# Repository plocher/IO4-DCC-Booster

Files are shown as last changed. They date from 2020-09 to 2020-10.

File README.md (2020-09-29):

# IO4-DCC-Booster
## License: CERN Open Hardware Licence v1.2

IO4 DCC Booster

A DIY DCC booster for a BOM cost of about $20 when using bulk China/eBay parts.

I was working on designing a motor shield using the $10 IBT-2
H-Bridge when I came across the work done by D. Bodnar at
[train electronics.com](http://www.trainelectronics.com/DCC_Arduino/DCC_Booster/)

I wanted to use one of these for every control point on my layout
instead of a DCC circuit breaker + booster power district mashup.
As the DCC Breakers are at least double the DIY cost for these
dedicated boosters, and I will end up with 10-20 control points on
my SPCoast layout, the savings might actually cover the development
costs :-)

These boosters DO NOT support auto-reverse, and the sketch software
doesn't try to do soft start detection of sound decoder capacitor
inrush currents.  Since there will be on average a single train
powered by each of these boosters on my N-Scale layout, I don't
expect this to be a real issue.  In practice, a simple 1 or 2 amp
unit would probably be good enough; at 5 to 6 amps, this is overkill.

From the original web writeup at trainelectronics.com:

<blockquote>
Introduction

In addition to experimenting with DCC++ over the last few months I
have been trying out different H-Bridges to see if there is one
that would work with DCC++ while delivering more than the 1 to 2
amps that the standard Arduino Motor Shield provides.  Such a option
would a good option for G scale layouts that typically draw much
more power than smaller scales.

I came across a few higher power shields
[that are described here](http://trainelectronics.com/DCC_Arduino/DCC++/)
including one that has an advertised power capability of 43 amps.
While I am a bit skeptical about this claim my tests show that it
has no problem delivering 5 or more amps, more than enough for my
purposes.  I describe how this can be interfaced to the DCC++
controller in the link above.

In order to make the use of this H-Bridge more convenient I decided
to design a stand-alone DCC booster that would attach to a DCC
signal and boost it before powering a track.  The booster is designed
to work with DCC++, Digitrax and other systems.

Hardware - H-Bridge

The H-Bridge is available from eBay, Amazon and other vendors -
just search for "H-Bridge 43 amp BTS7960B".  Make sure you get the
unit that has two BTS7960B devices on it - each is 1/2 of an H-Bridge.
The control signals go to the 8 pins on the front and the power in
and power out wires go to the 4 pin screw terminal connector at the
rear.

This H-Bridge and similar units do not operate on the single PWM
signal that most DCC systems provide.  It needs a right hand rotating
PWM and a left hand PWM.  To change the single PWM signal to two a
simple one transistor circuit is needed.  That circuit can be seen
in the lower left corner of the schematic (below).

The H-Bridge can act as a DCC booster without much more than the
Opto Coupler circuit and the one transistor converter.  The H-Bridge
does hove an over current shutdown capability but it doesn't react
until well over 30 amps are being drawn, way more than we are going
to use.  To get around this problem so that the system shuts down
immediately if the track is shorted an Arduino Pro Mini has been
added.  The Arduino monitors the current sensing pin on the H-Bridge
and can turn it off should it detect a high reading.

</blockquote>

His prototype reused a board he had on hand; this project simply
turns his schematic into a purpose-built board - and adds remote control
(enable/disable and monitoring) via an IO-4 RJ12/6 interface.

The differences:
  * powered by (3.0) the IO-4 Jack / IOexpander and (3.1) by the DC booster power.
  * local control - a maintainer "disable track power" switch
  * remote control
    * enable/disable track power
  * remote feedback
    * enabled
    * occupied
    * overload
  * Loconet and NCE Booster Bus daisy chain command station cable jacks

=== Estimated BOM costs ===
:	$ 1.00  PCB 
:	$10.00  IBT-2 
:	$ 3.50  Pro Mini Clone
:	$ 0.45  6n137
:	$ 0.20  2200uF x2
:	$ 3.00  RJ and Phoenix connectors
:	$ 1.00  SPDT Switch
:	$ 1.00  R/C/LEDs
:	------
:      ~$20.00

The booster will also need a 12-18v 6A+ DC power supply; the logic and
feedback electronics are isolated from the power supply (using opto
isolator for the booster bus and a full wave bridge for the power
supply), so there should be no problems driving a set of boosters
from a single large amperage switching supply.

As with ALL high power systems, use a SLOW BLOW or POLYFUSE in your
power supply feed.  20v at 6A is 120W - similar to a very bright
and hot incandescent bulb, if you remember them.  You don't want
to arc weld or start a fire on your layout if something goes wrong!

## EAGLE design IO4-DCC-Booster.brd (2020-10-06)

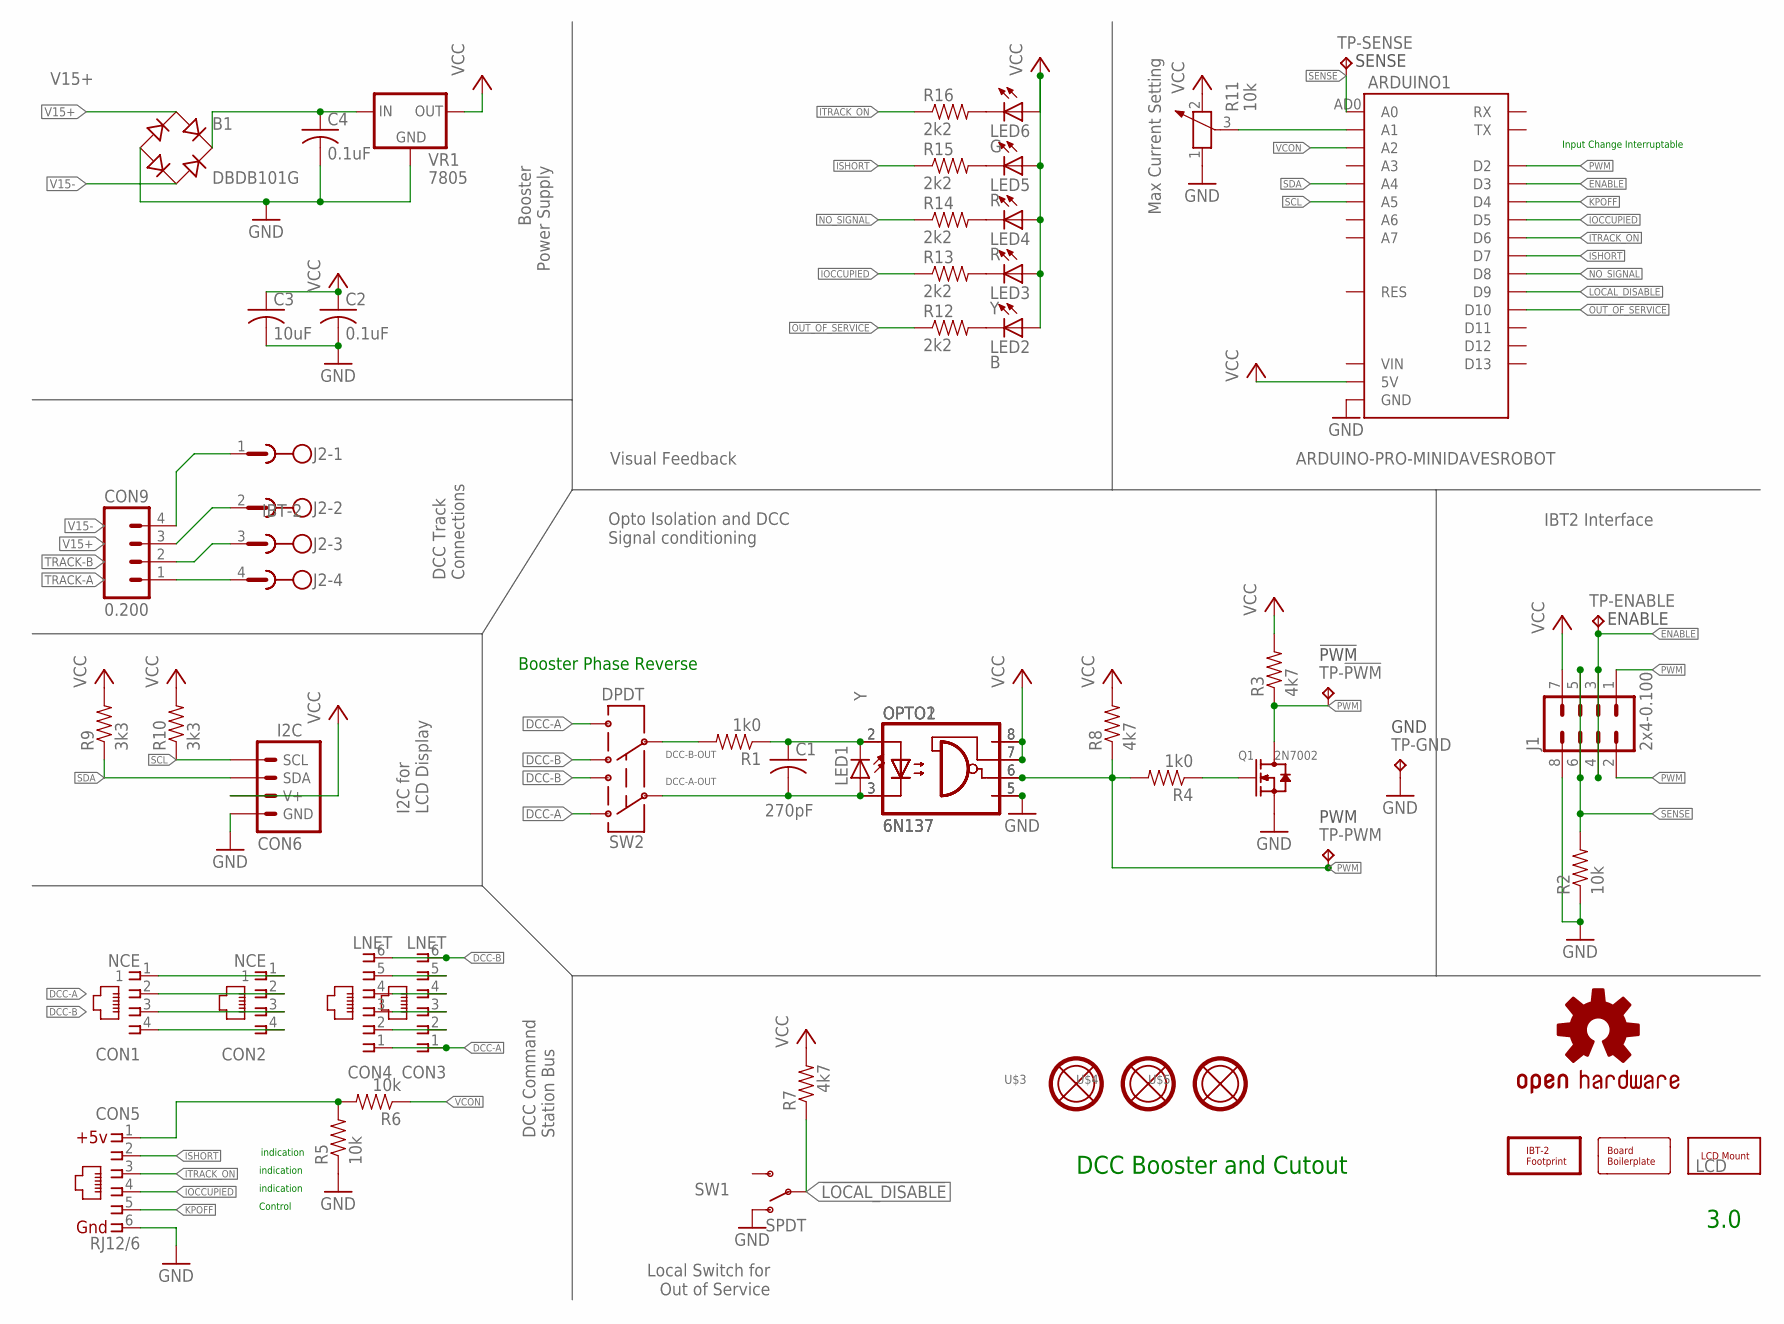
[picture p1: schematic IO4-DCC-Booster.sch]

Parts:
ARDUINO1: ARDUINO-PRO-MINIDAVESROBOT; ARDUINO_PRO_MINI_DAVEK
B1: DBDB101G; DB
BOARD1: BOARD100X100-NOHOLES; BOARD-SEEED10X10-NOHOLES
C1: 270pF; 0805-CAP
C2, C4: 0.1uF; 0805-CAP
C3: 10uF; 0805-CAP
CON1, CON2: NCE; 555980-1
CON3, CON4: LNET; RJ25-PANEL
CON5: RJ12/6; RJ25-PANEL
CON6: I2C; I2C-L
CON9: 0.200; MSTBA4
J1: 2x4-0.100; MA04-2
J2: IBT-2; MSTBA4
LCD: LCD; LCD-16X2-SILK
LED1, LED3: Y; 0603-LED
LED2: B; 0603-LED
LED4, LED5: R; 0603-LED
LED6: G; 0603-LED
LOGO1: DOC-OSHW-LOGO-L; OSHW-LOGO-L
OPTO1: 6N137; DIL08
OPTO2: 6N137; SM8
Q1: 2N7002; SOT23
R1, R4: 1k0; 0805-RES
R2, R5, R6: 10k; 0805-RES
R3, R7, R8: 4k7; 0805-RES
R9, R10: 3k3; 0805-RES
R11: 10k; B25X
R12, R13, R14, R15, R16: 2k2; 0805-RES
SW1: SPDT; SWITCH-SPDT-508
SW2: DPDT; 8X8-SQ-PB
TP-!PWM: TPPAD1-13; P1-13
TP-ENABLE: TPPAD1-13; P1-13
TP-GND: TPPAD1-13; P1-13
TP-PWM: TPPAD1-13; P1-13
TP-SENSE: TPPAD1-13; P1-13
U$2: IBT-2
U$3, U$4, U$5: MOUNTINGHOLE
VR1: 7805; TO-252

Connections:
!IOCCUPIED: ARDUINO1.D5, CON5.4, R13.1
!ISHORT: ARDUINO1.D7, CON5.2, R15.1
!ITRACK_ON: ARDUINO1.D6, CON5.3, R16.1
!KPOFF: ARDUINO1.D4, CON5.5
!LOCAL_DISABLE: ARDUINO1.D9, R7.1, SW1.2
!NO_SIGNAL: ARDUINO1.D8, R14.1
!OUT_OF_SERVICE: ARDUINO1.D10, R12.1
!PWM: J1.2, Q1.3 (D), R3.1, TP-!PWM.TP
DCC-A: CON1.2, CON2.2, CON3.1, CON4.1, SW2.1A, SW2.2B
DCC-A-OUT: C1.2, LED1.A, OPTO1.3 (C), OPTO2.3 (C), SW2.1C
DCC-B: CON1.3, CON2.3, CON3.6, CON4.6, SW2.1B, SW2.2A
DCC-B-LIMITED: C1.1, LED1.C, OPTO1.2 (A), OPTO2.2 (A), R1.1
DCC-B-OUT: R1.2, SW2.2C
ENABLE: ARDUINO1.D3, J1.3, J1.4, TP-ENABLE.TP
GND: ARDUINO1.GND@1 (GND), ARDUINO1.GND@2 (GND), ARDUINO1.GND@4 (GND), B1.-, C2.2, C3.2, C4.2, CON5.6, CON6.GND, CON6.GND@1 (GND), J1.8, OPTO1.5 (GND), OPTO2.5 (GND), Q1.2 (S), R2.1, R5.1, R11.1, SW1.1 (O), TP-GND.TP, VR1.2 (GND)
LIMIT: ARDUINO1.AD1 (A1), R11.3 (2)
unnamed: Q1.1 (G), R4.1
unnamed: CON1.4, CON2.4
unnamed: CON1.1, CON2.1
unnamed: CON3.5, CON4.5
unnamed: CON3.4, CON4.4
unnamed: LED4.C, R14.2
unnamed: CON3.3, CON4.3
unnamed: LED2.C, R12.2
unnamed: LED3.C, R13.2
unnamed: LED6.C, R16.2
unnamed: LED5.C, R15.2
unnamed: CON3.2, CON4.2
unnamed: B1.+, C4.1, VR1.1 (IN)
PWM: ARDUINO1.D2, J1.1, OPTO1.6 (VO), OPTO2.6 (VO), R4.2, R8.1, TP-PWM.TP
SCL: ARDUINO1.AD5 (A5), CON6.SCL, CON6.SCL@1 (SCL), R10.1
SDA: ARDUINO1.AD4 (A4), CON6.SDA, CON6.SDA@1 (SDA), R9.1
SENSE: ARDUINO1.AD0 (A0), J1.5, J1.6, R2.2, TP-SENSE.TP
TRACK-A: CON9.1, J2.4
TRACK-B: CON9.2, J2.3
V15+: B1.AC1, CON9.3, J2.2
V15-: B1.AC2, CON9.4, J2.1
VCC: ARDUINO1.5V, C2.1, C3.1, CON6.V+, CON6.V+@1 (V+), J1.7, LED2.A, LED3.A, LED4.A, LED5.A, LED6.A, OPTO1.7 (VE), OPTO1.8 (VCC), OPTO2.7 (VE), OPTO2.8 (VCC), R3.2, R7.2, R8.2, R9.2, R10.2, R11.2 (3), VR1.3 (OUT)
VCOMPUTER: CON5.1, R5.2, R6.2
VCON: ARDUINO1.AD2 (A2), R6.1

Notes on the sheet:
3.0
DCC Booster and Cutout
Control
indication
Input Change Interruptable
Max Current Setting
Visual Feedback
Booster Power Supply
DCC Track Connections
I2C for LCD Display
DCC Command Station Bus
Local Switch for Out of Service
Opto Isolation and DCC Signal conditioning
IBT2 Interface
Booster Phase Reverse

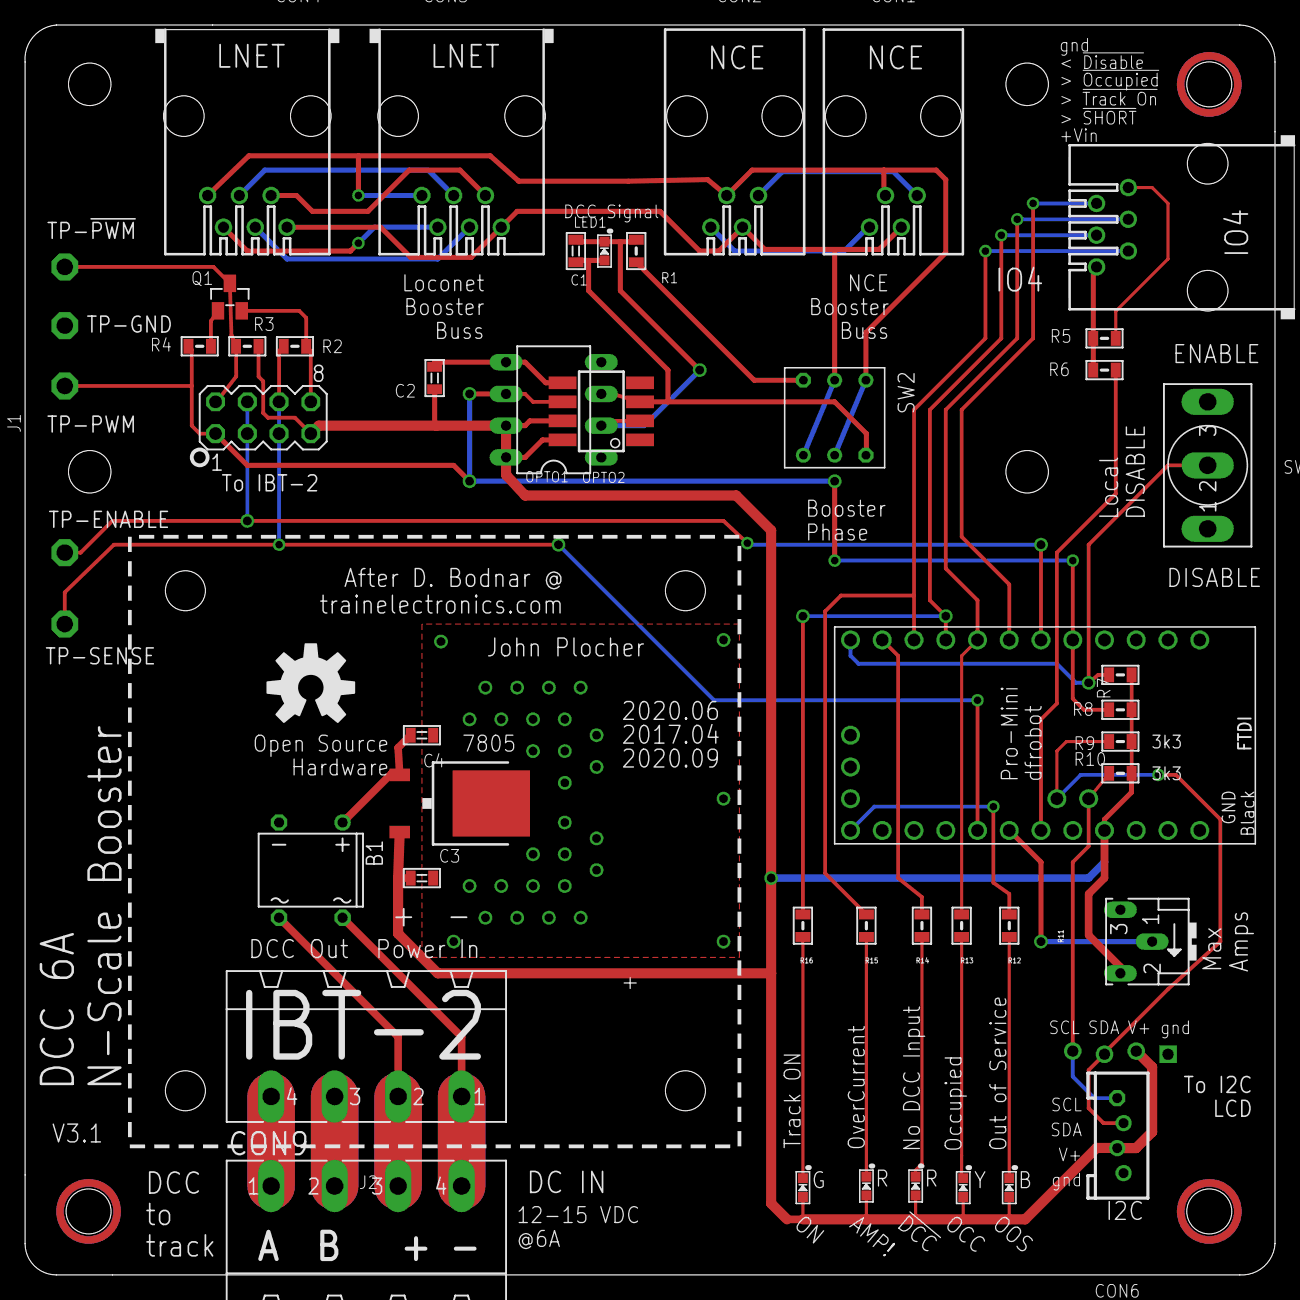
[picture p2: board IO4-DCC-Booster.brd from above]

Board: 2 copper layers, 100.0 x 100.0 mm, 55 parts (0 on the bottom side), 40 nets.

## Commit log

2020-09-29 Initial version
    [IO4-DCC-Booster.brd, IO4-DCC-Booster.sch]
2020-09-29 Rework, DC supply, simpler trace layout
    [IO4-DCC-Booster.brd, IO4-DCC-Booster.sch]
2020-10-06 normalized values
    [IO4-DCC-Booster.brd, IO4-DCC-Booster.sch]

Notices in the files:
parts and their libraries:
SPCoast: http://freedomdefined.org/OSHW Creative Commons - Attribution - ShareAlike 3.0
